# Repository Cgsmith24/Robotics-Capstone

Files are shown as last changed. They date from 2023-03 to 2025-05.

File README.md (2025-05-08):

Project TASRC


Designed and Engineered by: Chase Smith

Coded and Reported by: Chase Smith

Date: February 20th - May 10th 2023.

With Project TASRC, I had a vision, A vision of a car that could drive almost anywhere, perfectly smoothly. The car would be able to use 4 separate sensors for each wheel, and can sense the ground in front of each wheel, and would be able to adapt each individual arm to accommodate the terrain it was given. Unfortunately, due to time constraints, and hardware limitations. I was not able to achieve this dream to what it could truly be. Due to the processing power limitations of an arduino, and time limitations, I was unable to get all 4 sensors to function properly, So, the solution was to have 2 sensors, one for the front, and one for the rear. Nevertheless with the issues I have, I believe that I have achieved my goal to a great extent. 

The system uses two ultrasonic sensors connected to an arduino mega, each sensor controls two servos, two for the front, and two for the rear. The servos control a double wishbone suspension arm, this system is useful because no matter how the suspension moves, the wheels will stay vertical. If I don’t have this system, the more you raise and lower the suspension, the more the wheels would tilt in or out, effectively giving you camber, which for a car meant to crawl over things isn't the best idea.

The whole car is made up of custom made parts, the only structural parts that aren’t printed are the main chassis, and the upper chassis. The main chassis is made of an aluminum alloy bar that gives many mounting holes. The upper chassis is just a cut piece of cardboard, it is not structural, it is only used as a place to put micro controllers and battery packs. Every 3D printed part (with the exception of the ultrasonic sensor holders) was designed and printed by me on my basic Ender 3 3D printer. Every part is printed in PLA. The parts are printed in PLA so that they are cheap, reliable, and easy to print. The infill is low where it needs to be to support structure. But low where it doesn’t need to be as strong, all this combined means that I can have lots of prints for a low gram count. 
F

Design Evaluation.

If I'm being strict on the design, it has a lft left to be desired. Originally the plan was to have an actual mechanical steering system, there are 3d designs in the 3D files folder for a mechanical steering assembly. The design could be reformed, with lifted headers, full soldering of every wire, not using cardboard. But due to my time and project limitations, I think it turned out very good. If I could do this project again without my previoud limitations, I would try to 3D print every part that could be printed. For Example: No cardboard, instead a 3D Printed Slab, no metal for motor or chassis, EVERYTHING 3D printed. I will most likely revise this in the future. 

Functional Categories

Output Display: The output display is very simple, there are 2 LEDS, 1 green one, and one red one. The 1 green one turns on when the suspension system is not moving, sensing, but not moving, meaning that it has reached an acceptable range. The red LED is built into the rc receiver, it shows when the remote is connected to the car, and when input is being given.

Manual User Input: Manual User input is given in two ways, there is a controller that I pulled from an old rc car that isn’t worth much. The left stick controls the left side of the car, and the right side controls the right side. There is also a switch that can lock up the suspension system, so you can just ride around with no suspension, this is ideal for flat surfaces.

Automatic sensor: The automatic sensors are just 2 ultrasonic sensors, and  one for the front and one for the rear. These sensors record distance to the ground and tell the servos controlling the suspension to move based on that distance.

Actuators, Mechanisms, and Hardware: Three are 4 servos, one for each arm, 4 motors, one for each wheel. Physical mechanisms are: Double wishbone suspension front and rear. Each servo has its own shock connected to a servo horn, which is then connected to the arm for control of the arm. Hardware: There is an Arduino mega to control the entirety of the suspension system, the mega is needed due to the insane amount of wires and connections needed to control the suspension. There is also an Arduino Nano to control the entirety of the Drive system. There is a FLYSKY radio, and a KYOSHO Receiver, that is connected to the Nano, with one channel running to the mega to lock up suspension. There are two 6 volt power packs, not wired in series or in parallel, they are wired completely separate from each other, one power pack powers all the servos and sensors. And one powers both microcontrollers and the receiver.

Logic, Processing, and Control: The logic behind the suspension sounds simple, but actually is quite complicated. The sensors send an ultrasonic pulse to the ground, and it bounces back, the time between these two processes determines the distance to the ground. This happens 20 times a second. Then you have to take that time reading, and convert it to centimeters. After that you have to take that centimeter reading, and convert it to angle adjustments to the servos. So with this complicated process, you have to convert time to angles (Crazy, right). 
	I also have 2 Microcontrollers processing and completing two separate functions. The second controller is an Arduino Nano, this one is necessary because when you tell an arduino to use radio signals, it takes over every other function of the arduino. Meaning I could not possibly use one arduino for this whole project. The nano receives 2 signals from the remote, one for the left side drive, and the other for the right side drive. 

Parts List

Lessons Learned

An arduino mega has a hard time controlling more than 4 servos and 2 distance sensors, so I had to switch to only 2 sensors.
An arduino when connected to a radio signal, blocks any other functions from occurring, So I had to integrate another arduino to use the radio signals.
Steering is hard, and I was running out of time. I had originally planned to have a real steering assembly. But I was running out of time, So I switched to tank drive. 
PLA can be brittle when not printed correctly. So I had to redesign and reprint the arms a few times to get ones strong enough to do the job.
A single battery pack can only do so much. I had to use 2 of them to get the project to have enough power.
Ultrasonic sensors are actually incredibly accurate, any minor movement would cause them to tell the servos to readjust, and that would just cause a chain reaction and make the robot go crazy, so I added an acceptable distance for the sensors to read, which fixed the problem. 



Build it Yourself

What you need:

A 3D Printer capable of printing PLA

200 Grams of PLA 3d Printing materials

A computer capable of a 3D slicer, and capable of Arduino IDE.

Solder

Soldering Iron

4 standard size servos

4 Arduino Motors and wheels

L298N Motor Controller

1 Arduino Mega 2560 (A normal UNO may work but not guaranteed)

1 Arduino Nano

2 5 AA power packs

2 HC-SR04 Ultrasonic sensors

Any RC remote and receiver

A piece of metal/plastic to make the main chassis

Cardboard

Hot Glue

Tons of wires

PATIENCE!!!

Step one: Printing

Print the following parts found on my github:

TASRC A-arm_fixed.stl x4

TASRC Turnbuckle V2.stl x4

TASRC Shock Tower V3.stl x2

TASRC Rear Hub Right_fixed.stl x2

TASRC Rear Hub Left_fixed.stl x2

TASRC Shock Tensioner.stl x4

Ultrasonic_HC-SR04_-_FOOT_MOUNT.stl x2

Step Two: Wiring



Once you have all the parts printed described in step one, get all your materials together.  And look at the wiring diagram shown in the Github, and wire all your systems like that. 

Yes, it looks like spaghetti, but it works. 

Step 3: Assembly
In the 3D Files folder in the github, open FULL_BUILD.stl, that will show how all the parts interlock with each other, use whichever hardware you want to hold it all together. It is not shown in the 3D file, but the sensor holder holes match up with the holes that hold the arms to the shock tower, so just put your screws through that. Also not shown in the stl, is that you need to put a piece of cardboard on top of the servos, I just hot glued a cut piece of cardboard. That is where you mount your aduinos, power pack, and RC receiver, it doesn’t matter where you mount them, as long as you are happy with the placements. Once you have all that done, you can attach the wheels, I just used some metal bars and hot glue to attach them. 

Step 4: Coding

On the ardunio mega, upload the code Suspension_Code.ino, and upload to the Arduino nano Drive_Code.ino. Adjustments to code may need to be made in order to get it to function properly on your build.

Step 5: Testing/Trial and Error

From this point forward, it’s just testing and trial/error. It may take lots of testing to get it to work.  But with some time and effort, I guarantee you can do it!

Conclusion:

I hope you enjoy the struggles of this project. If you have any questions about this project, Email me at chasegsmith22@gmail.com

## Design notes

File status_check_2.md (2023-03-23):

2: Project TASRC has used 150g of filament to date, 5 servos, some aliuminum, 4 shocks, and roughly 40$ in the budget.
3: I need to get some better wheels, I don't need to print anything else as of right now. The only system that has yet to be designed is the steering, 
But I already have an idea about how to do that. 
I will demonstrate the steering colum and the 4 shocks moving on left/right controls.

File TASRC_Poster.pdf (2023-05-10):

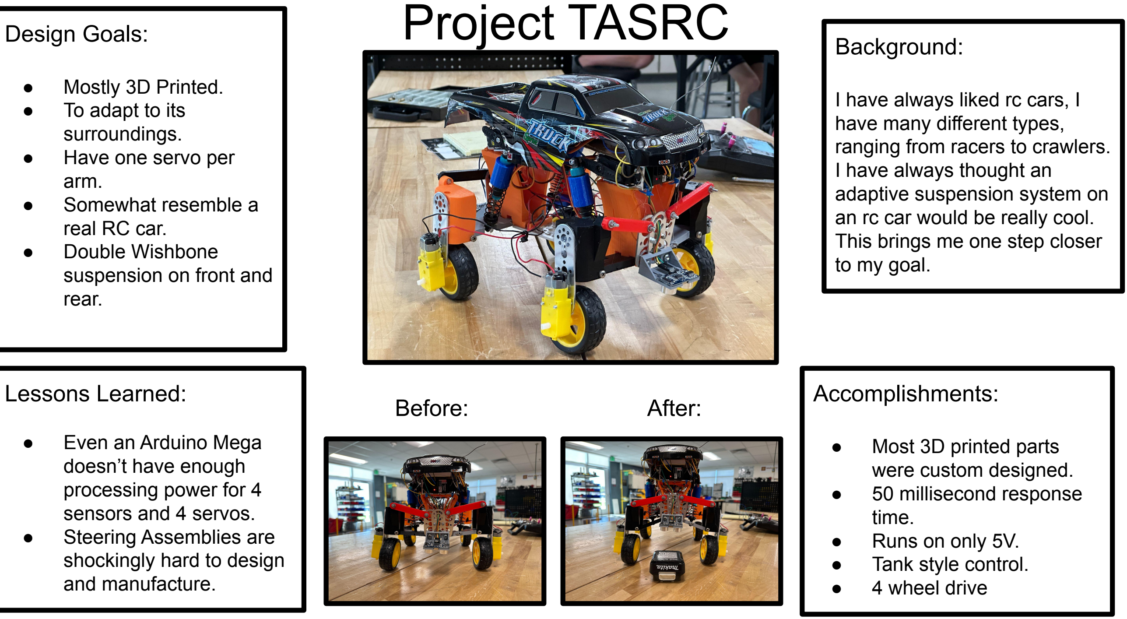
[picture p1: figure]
Design Goals:; Project TASRC; ● Mostly 3D Printed. ● To adapt to its surroundings. ● Have one servo per arm. ● Somewhat resemble a real RC car. ● Double Wishbone suspension on front and rear.; Lessons Learned:; ● Even an Arduino Mega doesn’t have enough processing power for 4 sensors and 4 servos. ● Steering Assemblies are shockingly hard to design and manufacture.; Background:; I have always liked rc cars, I have many different types, ranging from racers to crawlers. I have always thought an adaptive suspension system on an rc car would be really cool. This brings me one step closer to my goal.; Accomplishments:; ● Most 3D printed parts were custom designed. ● 50 millisecond response time. ● Runs on only 5V. ● Tank style control. ● 4 wheel drive; Before:; After:

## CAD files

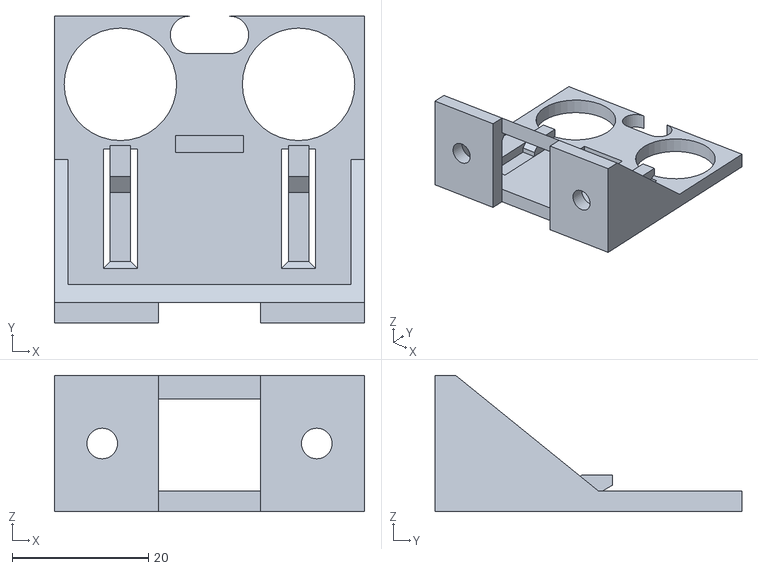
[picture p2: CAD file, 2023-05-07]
3D_Files/Ultrasonic_HC-SR04_-_FOOT_MOUNT (1).stl
45.5 x 45.0 x 20.0

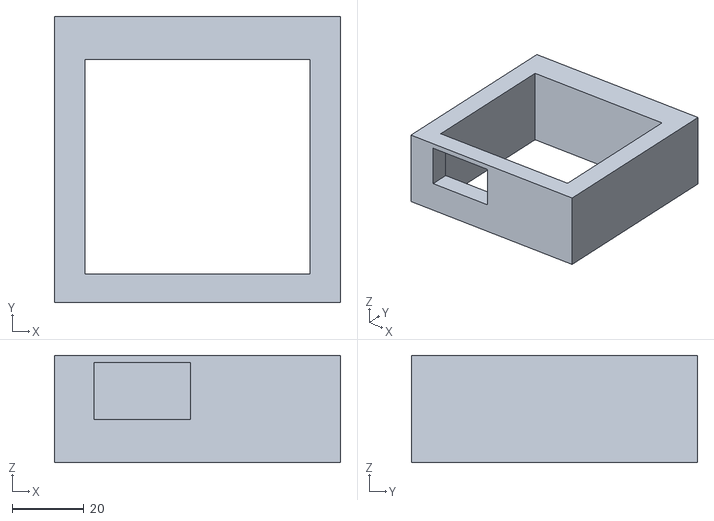
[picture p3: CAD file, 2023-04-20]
3D_Files/Battery_holdster.stl
80.0 x 80.0 x 30.0

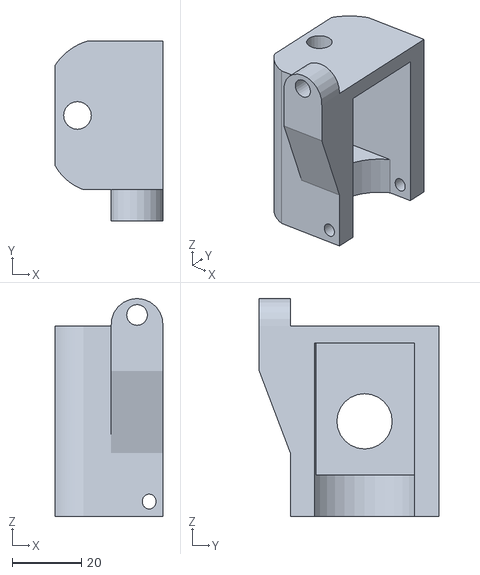
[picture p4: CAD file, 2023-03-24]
3D_Files/TASRC Rear hub Left_fixed.stl
31.2 x 52.0 x 63.1

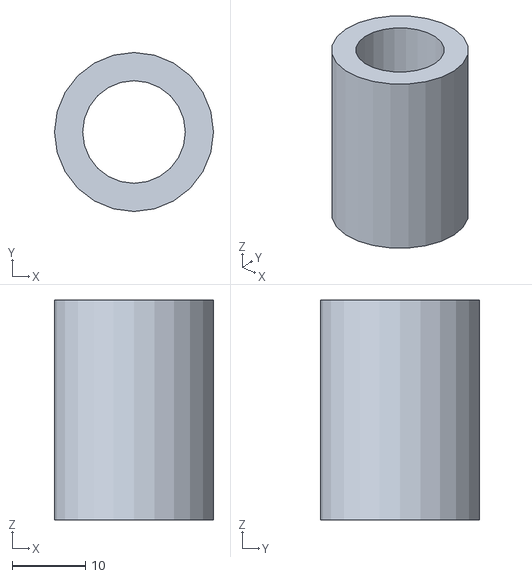
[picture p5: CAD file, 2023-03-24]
3D_Files/TASRC Shock Tensioner.stl
21.7 x 21.7 x 30.0

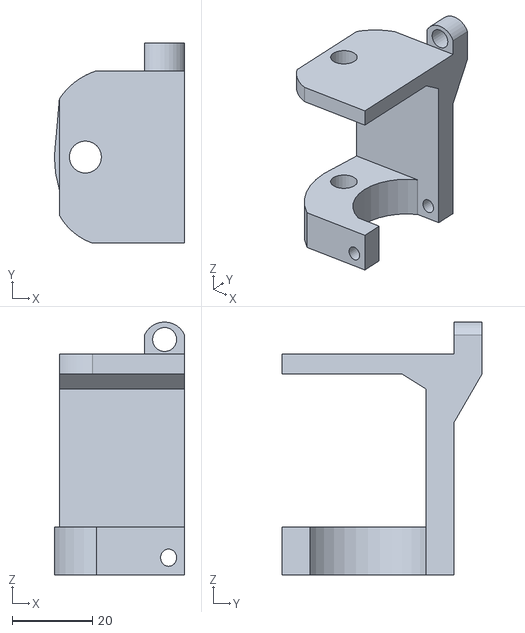
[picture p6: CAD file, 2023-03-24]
3D_Files/TASRC Front hub Left_fixed.stl
32.5 x 50.0 x 63.1

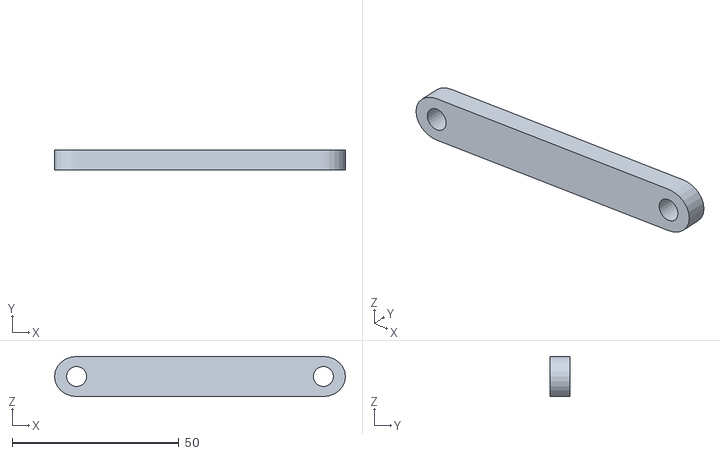
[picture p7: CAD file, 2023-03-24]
3D_Files/TASRC Turnbuckle.stl
87.1 x 6.00 x 12.0

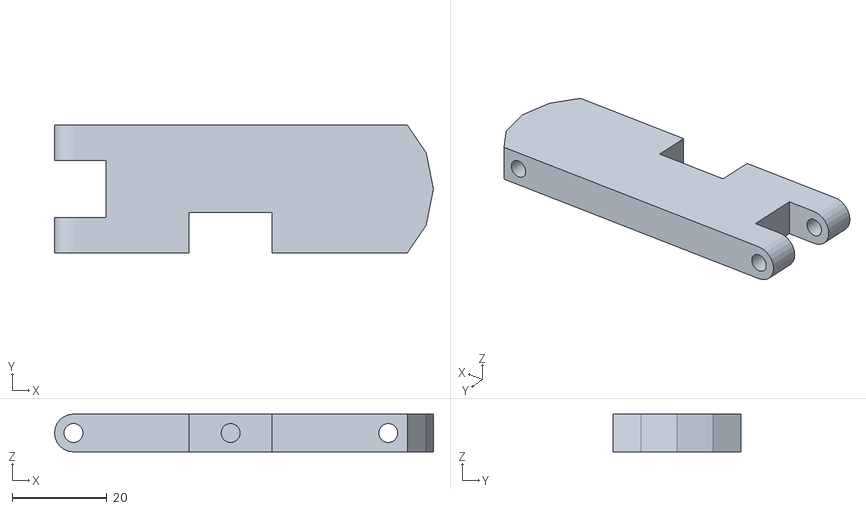
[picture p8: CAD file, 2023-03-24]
3D_Files/TASRC A-arm_fixed.stl
79.9 x 27.0 x 8.00

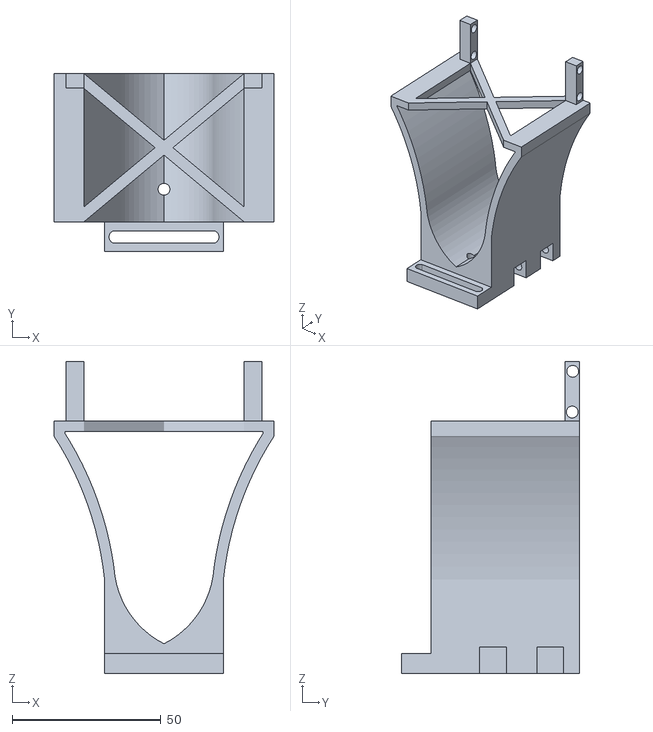
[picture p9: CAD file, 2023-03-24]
3D_Files/TASRC Shock Tower V3.stl
74.0 x 60.0 x 105.0

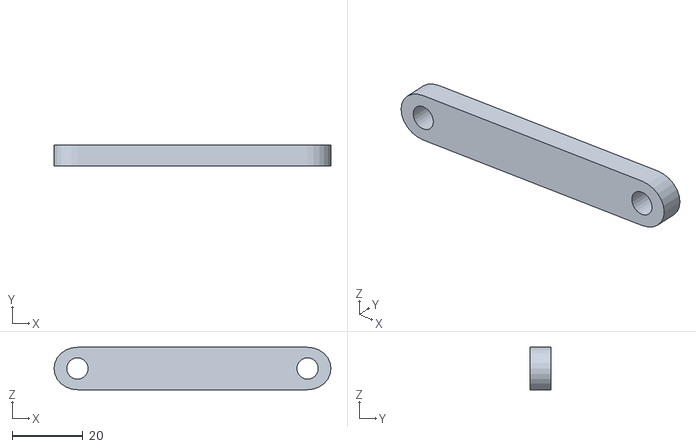
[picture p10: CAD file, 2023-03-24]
3D_Files/TASRC TurnBuckle V2.stl
78.1 x 6.00 x 12.0

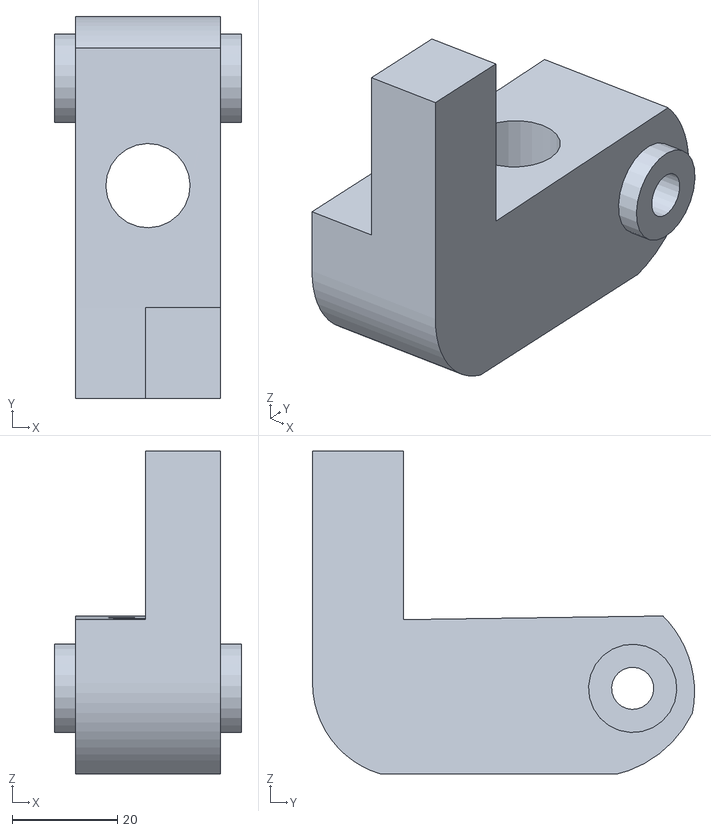
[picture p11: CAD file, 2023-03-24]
3D_Files/TASRC Turning Link Right_fixed.stl
35.6 x 72.5 x 61.3

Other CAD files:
3D_Files/TASRC Rear hub Right_fixed.stl
3D_Files/TASRC Front hub Right_fixed.stl

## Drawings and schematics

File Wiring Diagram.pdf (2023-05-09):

### I mya

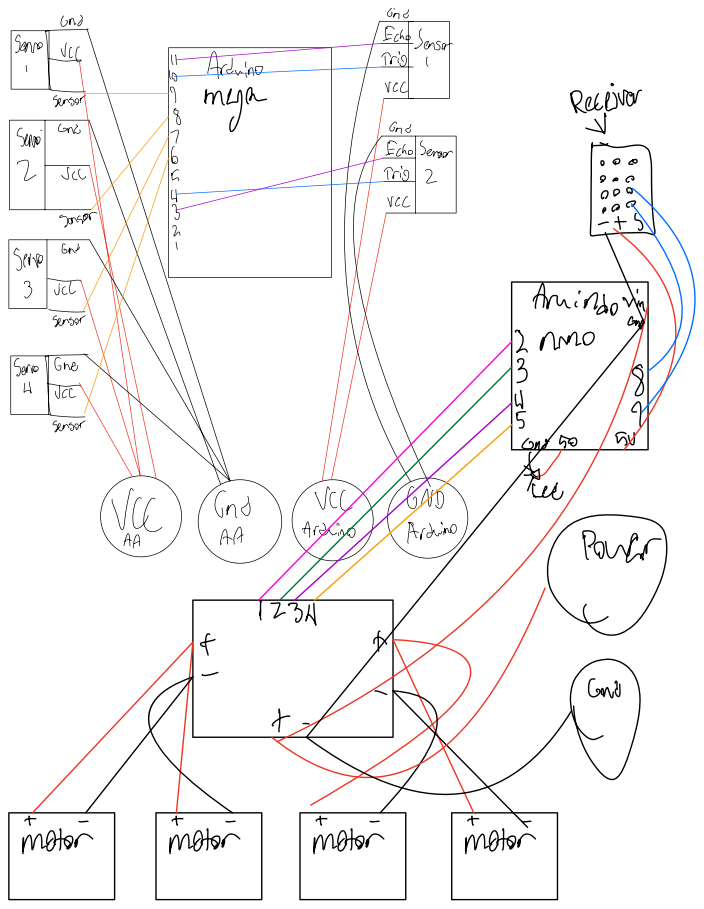
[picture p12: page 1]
and; MEI; Arduino; rec; Gnc; and É ve; Sensor; Serve; Amindovin; 2 Amo; segue; GND; VG Cnd; Arduin; motor

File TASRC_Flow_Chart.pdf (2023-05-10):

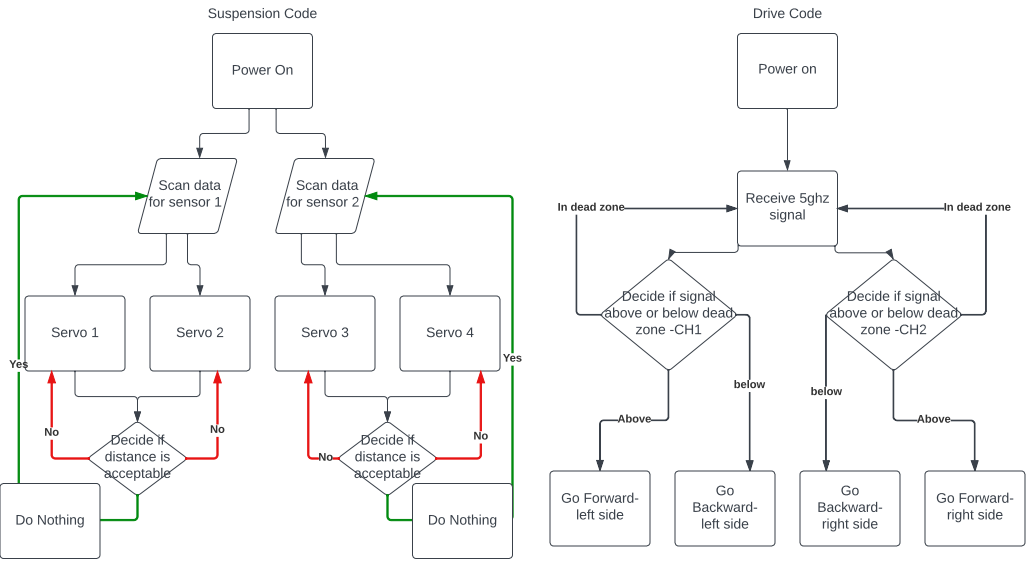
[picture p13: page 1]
Power On; Suspension Code; Scan on Sensor 2; Servo 1; Servo 2; Servo 3; Servo 4; Power on; Drive Code; Scan data for sensor 1; Scan data for sensor 2; Decide if distance is acceptable; Yes; Do Nothing; Receive 5ghz signal; Above; below; Go Forward- left side; Go Forward- right side; Go Backward- left side; Go Backward- right side

In dead zone

Decide if signal
above or below dead
zone -CH1

zone -CH2

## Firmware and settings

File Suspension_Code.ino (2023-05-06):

#include <Servo.h>

#define TRIG_PIN1 10
#define ECHO_PIN1 11
#define TRIG_PIN2 4
#define ECHO_PIN2 3

Servo servo1;
Servo servo2;
Servo servo3;
Servo servo4;


int servoPin1 = 9;
int servoPin2 = 8;
int servoPin3 = 7;
int servoPin4 = 6;
int servoPos1 = 90;
int servoPos2 = 90;
int servoPos3 = 90;
int servoPos4 = 90;

float minGoalDistance1 = 4.0; // Set the minimum goal distance for sensor 1 to 6cm
float maxGoalDistance1 = 5.0; // Set the maximum goal distance for sensor 1 to 7.5cm
float minGoalDistance2 = 5.0; // Set the minimum goal distance for sensor 2 to 8cm
float maxGoalDistance2 = 6.0; // Set the maximum goal distance for sensor 2 to 9.5cm

void setup() {
pinMode(TRIG_PIN1, OUTPUT);
  pinMode(ECHO_PIN1, INPUT);
  pinMode(TRIG_PIN2, OUTPUT);
  pinMode(ECHO_PIN2, INPUT);


  servo1.attach(servoPin1);
  servo1.write(servoPos1);
  
  servo2.attach(servoPin2);
  servo2.write(servoPos2);
  
  servo3.attach(servoPin3);
  servo3.write(servoPos3);
  
  servo4.attach(servoPin4);
  servo4.write(servoPos4);
  
  Serial.begin(9600);

}
void loop() {
  // Send ultrasonic pulse for sensor 1
  digitalWrite(TRIG_PIN1, LOW);
  delayMicroseconds(2);
  digitalWrite(TRIG_PIN1, HIGH);
  delayMicroseconds(10);
  digitalWrite(TRIG_PIN1, LOW);

  // Receive echo and calculate distance for sensor 1
  long duration1 = pulseIn(ECHO_PIN1, HIGH);
  float distance1 = duration1 / 58.0;

  // Send ultrasonic pulse for sensor 2
  digitalWrite(TRIG_PIN2, LOW);
  delayMicroseconds(2);
  digitalWrite(TRIG_PIN2, HIGH);
  delayMicroseconds(10);
  digitalWrite(TRIG_PIN2, LOW);

  // Receive echo and calculate distance for sensor 2
  long duration2 = pulseIn(ECHO_PIN2, HIGH);
  float distance2 = duration2 / 58.0;

  Serial.print("Distance 1: ");
  Serial.print(distance1);
  Serial.println(" CM");

  Serial.print("Distance 2: ");
  Serial.print(distance2);
  Serial.println(" CM");

  // Check if distance is within the acceptable range for sensor 1
  if (distance1 >= minGoalDistance1 && distance1 <= maxGoalDistance1) {
    // Do nothing if distance is within acceptable range for sensor 1
  } else {
    // Calculate the difference between the current distance and the goal distance for sensor 1
    float distanceDiff1 = (distance1 < minGoalDistance1) ? minGoalDistance1 - distance1 : distance1 - maxGoalDistance1;

    // Move servos 1 and 2 to adjust the height of the car for sensor 1
    if (distance1 < minGoalDistance1) {
      // Move servos 1 and 2 down to lower the car for sensor 1
      servoPos1 += 5;
      if (servoPos1 > 180) {
        servoPos1 = 180;
      }

      servoPos2 -= 5;
      if (servoPos2 > 180) {
        servoPos2 = 180;
      }
    } else {
      // Move servos 1 and 2 up to raise the car for sensor 1
      servoPos1 -= 5;
      if (servoPos1 < 0) {
        servoPos1 = 0;
      }

      servoPos2 += 5;
      if (servoPos2 < 0) {
        servoPos2 = 0;
      }
    }

    // Set the new positions for servos 1 and 2 for sensor 1
    servo1.write(servoPos1);
    servo2.write(servoPos2);
  }
// Control servo 3 and servo 4 based on the readings from the second ultrasonic sensor
 if (distance2 >= minGoalDistance2 && distance2 <= maxGoalDistance2) {
    // Do nothing if distance is within acceptable range for sensor 1
  } else {
    // Calculate the difference between the current distance and the goal distance for sensor 1
    float distanceDiff2 = (distance2 < minGoalDistance2) ? minGoalDistance2 - distance2 : distance2 - maxGoalDistance2;

 
  if (distance2 < minGoalDistance2) {
    // Move both servos down to lower the car
    servoPos3 += 5;
    if (servoPos3 > 180) {
      servoPos3 = 180;
    }
    
    servoPos4 -= 5;
    if (servoPos4 > 180) {
      servoPos4 = 180;
    }
  } else {
    // Move both servos up to raise the car
    servoPos3 -= 5;
    if (servoPos3 < 0) {
      servoPos3 = 0;
    }
    
    servoPos4 += 5;
    if (servoPos4 < 0) {
      servoPos4 = 0;
    }
  }
  
  // Set the new positions for servos for second sensor
  servo3.write(servoPos3);
  servo4.write(servoPos4);


delay(100);  }}

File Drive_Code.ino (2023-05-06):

const int leftMotorForward = 2;
const int leftMotorBackward = 3;
const int rightMotorForward = 4;
const int rightMotorBackward = 5;

int leftTrigger = 8;
int rightTrigger = 9;

void setup() {
  Serial.begin(9600);
  
  pinMode(leftMotorForward, OUTPUT);
  pinMode(leftMotorBackward, OUTPUT);
  pinMode(rightMotorForward, OUTPUT);
  pinMode(rightMotorBackward, OUTPUT);
  
  pinMode(leftTrigger, INPUT);
  pinMode(rightTrigger, INPUT);
}

void loop() {
  int leftValue = pulseIn(leftTrigger, HIGH);
  int rightValue = pulseIn(rightTrigger, HIGH);
  
  Serial.print("Left: ");
  Serial.println(leftValue);
  
  Serial.print("Right: ");
  Serial.println(rightValue);
   if (rightValue > 1700) {
     digitalWrite(leftMotorForward, HIGH);
    digitalWrite(leftMotorBackward, LOW);
    digitalWrite(rightMotorForward, LOW);
    digitalWrite(rightMotorBackward, HIGH);
  } else if (rightValue < 1200) {
    digitalWrite(leftMotorForward, LOW);
    digitalWrite(leftMotorBackward, HIGH);
    digitalWrite(rightMotorForward, HIGH);
    digitalWrite(rightMotorBackward, LOW);
  } else {
   
    if (leftValue > 1700) {
    digitalWrite(leftMotorForward, LOW);
    digitalWrite(leftMotorBackward, HIGH);
    digitalWrite(rightMotorForward, LOW);
    digitalWrite(rightMotorBackward, HIGH);
  } else if (leftValue < 1200) {
    digitalWrite(leftMotorForward, HIGH);
    digitalWrite(leftMotorBackward, LOW);
    digitalWrite(rightMotorForward, HIGH);
    digitalWrite(rightMotorBackward, LOW);
  } else {
    digitalWrite(leftMotorForward, LOW);
    digitalWrite(leftMotorBackward, LOW);
     digitalWrite(rightMotorForward, LOW);
    digitalWrite(rightMotorBackward, LOW);
  }
  
  }
  delay(10);
}
